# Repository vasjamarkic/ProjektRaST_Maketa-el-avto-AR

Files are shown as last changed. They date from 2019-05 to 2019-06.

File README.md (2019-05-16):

# ProjektRaST_Maketa-el-avto-AR
Projekt izdelave makete električnega vozila z LI-ion celicami in obogateno resničnostjo
ekipa
Z izdelavo makete smo začeli v novembru 2018, ko smo uspešno prijavili projekt na razpis RaST. Za delovanje 5 kW BLDC motorja smo načrtoval baterijski sistem z 140 Li-ion celicami, vezani v 10p14s konfiguraciji. Vse pridobljene celice iz odrabljenih prenosnikov, powerbank-ov in e-koles smo z Voltcraft merilcem temeljito testirali (polnjenje, praznjenje, polnjenje, notranja upornost, pregrevanje) in slabe izločili, dobre pa presortirali v skupine po podobnih kapacitetah. Nakup EV opreme je bil opravljen pri dobavitelju Miromax (Latvija), ostala oprema pa na eBay-u in lokalnih tehničnih trgovinah. Visokonapetostni sklop ima največjo napetost 58,8 V, zato smo izbrali polnilec takšne napetosti in motor s krmilnikom do napetosti 72 V. Sistem smo z glavno varovalko (ETI) omejili na 125 A, dodatno pa krmilnik sprogramirali na še nižji tok obratovanja. Krmilnik in motor vklopimo z obratom ključa na pozicijo M oziroma II; tako vklopimo glavni kontaktor, ki premosti napetost B+ baterijskega sklopa na krmilnik preko BMS enote. Tako na poziciji ključa I in II zunanji rele vklopi MCU (main control unit), to je glavna kontrolna enota ali računalnik avta/makete, kjer krmilnimo luči, varnostne sisteme, merimo temperature, napetosti 12V sistema ter B+ baterijskega sklopa motorja (preko IL300 linearnega optičnega pretvornika), vklapljamo/izklapljamo BMS, upravlja z Nextion display-om in komunicira z Raspberry PI (UART protokol) in krmilnikom motorja (SPI - CANbus modul za pretvorbo podatkov). Za vse to smo uporabili preprost Arduino UNO. V MCU-ju deluje samostojno Micro:bit razvojna ploščica, ki ima g-senzor za detekcijo trka; le ta izključi celoten pogonski sklop (izklopi glavni kontkator). Sistem ima še varnostno stikalo ob priključitvi AC kabla za napajanje (recharge) baterij ter "emergency stop" oz. odklopnik, ki ga lahko uporabnik sam ročno sproži v primeru nevarnosti. BMS enota poleg merjenja napetosti posemznih serij celic in temperatur seveda skrbi za varno delovanje pogona in omeji morebitne preobremenitve (tokovne, temperaturne, napetostne). Raspberry PI zbira vse podatke iz Arduina ter jih brezžično (WiFi) pošilja usmerjevalniku. Le ta ima nalogo, da podatke naprej posreduje odjemalcem; to so lahko pametni telefoni uporabnikov, s katerimi na maketi v povečani resničnosti (agumented reality ali AR) opazujejo v realnem času parametre na maketi in/ali spoznavajo delovanje in lastnosti/specifikacije posameznega sklopa EV (electric vehicle) oziroma makete.  
Na tej povezavi je prikazan proces izdelave makete - od načrtovanja, do izgradnje in preizkušanja:
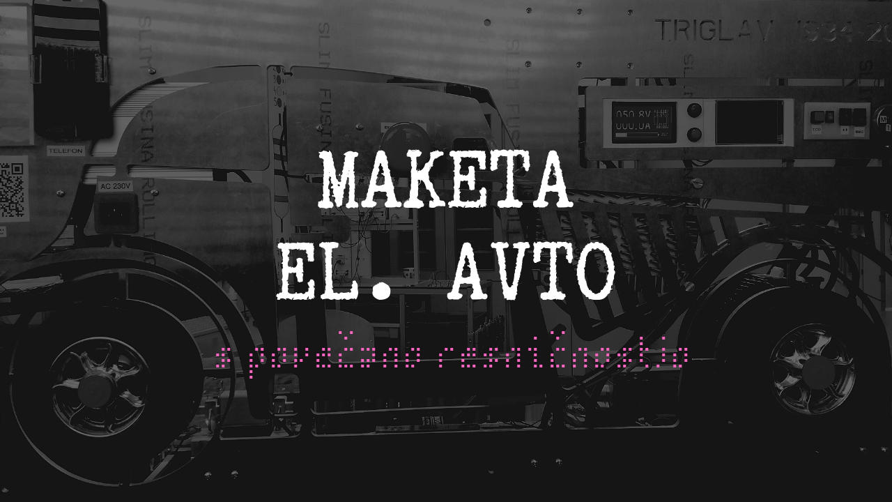
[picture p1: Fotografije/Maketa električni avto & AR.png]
IMAGE ALT TEXT (https://www.youtube.com/watch?v=B8ciZN42plY "Maketa el. avto")

Na spletni strani Srednje tehniške in poklicne šole Trbovlje je objavljen tudi opis projekta:
https://www.stps-trbovlje.si/category/rast/.

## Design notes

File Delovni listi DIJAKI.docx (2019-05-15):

# #rast – maketa el. avtomobila - NALOGE

## Arduino

### 1. Povezava med MCP2515 CAN/SPI modulom in Arduino Uno

a. Povežite pine Arduina Uno s pini modula MCP2515 CAN/SPI - izdelajte ustrezne priključke:

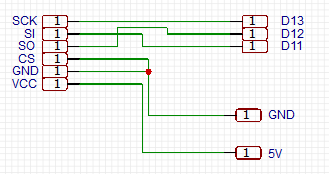
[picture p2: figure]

- 1x3p za priklop na Arduino,
- 1x6p ženski za MCP2515).
- 1x1p GND ženski,
- 1x1p 5V moški.

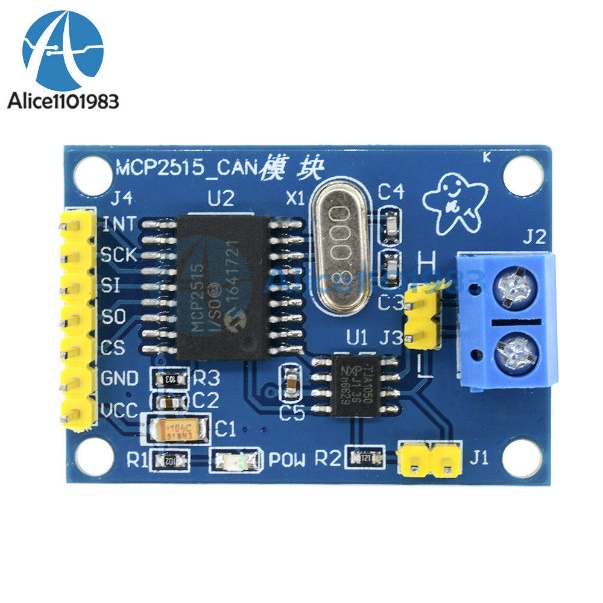
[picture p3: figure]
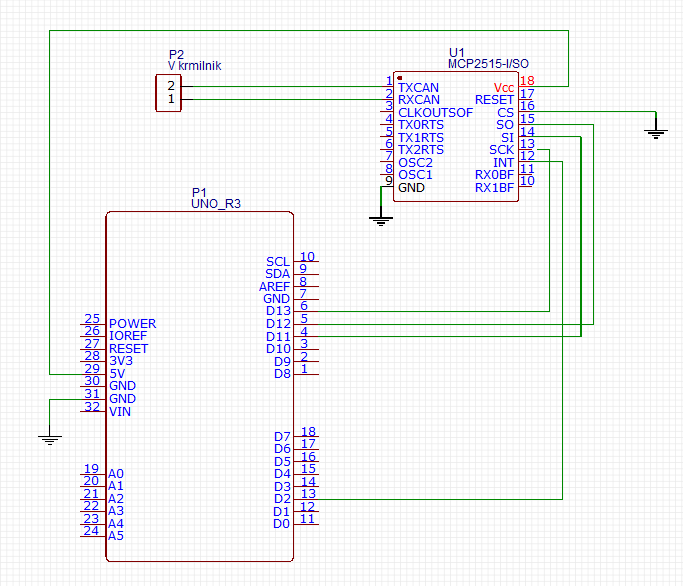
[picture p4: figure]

Vcc – 5 V; GND – GND; CS – GND; MISO – pin 12; MOSI – pin 11; SCK – pin 13

Opravljeno

b. Ustrezno podaljšajte CAN vodilo iz krmilnika motorja (uporabite dve žici in božirki) ter ga preko uvodnice vstavite v električno omarico. Na koncu namestite 2-pinski ženski konektor, ki paše na H-L moška pina modula MCP2515.

Opravljeno

c. Ustrezno sprogramirajte kodo Arduina, da bo lahko preko CAN vodila prejemal podatke iz krmilnika motorja. Primer inicializacija povezave SPI in CAN: [1] https://www.14core.com/wiring-the-mcp2515-controller-area-network-can-bus-diagnostics/

[2] https://www.electronicshub.org/arduino-mcp2515-can-bus-tutorial/a

Ni opravljeno

### 2. Vklop/izklop BMS-a z relejem z menjalnim stikalom na panelni plošči.

BMS se vklopi, ko je stikalo sklenjeno 3 sekunde, izključimo ga pa tako, če je stikalo sklenjeno 5 sekund. Za to bomo uporabili dvopoložajno stikalo: Arduino bo prebral stanje in krmilil rele, ki bo ustrezen čas sklenil »stikalo« BMS-a. Pozicija I – vklop BMS-a, pozicija II – izklop BMS-a. Stikalo ima tudi nevtralno pozicijo, katerega bomo vedno postavili takoj, ko bomo BMS vključili oz. izključili. Ker pa bi uporabnik na to pozabil, bi vključenost stikala na poziciji I ali II ne vplivala na ponovno aktivacijo releja za vklop/izklop BMS-a.

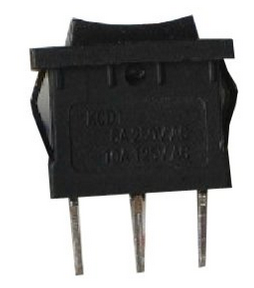
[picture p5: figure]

Na dig. vhoda (pin 6 in 7) Arduina povežemo skrajna priključka dvopoložajnega stikala (uporabite 2-polni moški konektor), sredinski priključek povežite na GND (0 V). Arduino pinout lastnost naj bo PULL_UP, torej ga proži GND brez pull-up uporov. V programu ustrezno definirajte oba digitalna pina kot vhod.

IN vhod releja priključite na pin 4 Arduina in ga definirajte kot izhod. Priključek DC+ releja vežete na +12V, DC- pa na GND. Na drugi strani releja povežete COM ter N.O. na priključke tipke BMS-a. Izvorno tipko BMS-a ohranimo!

vklop GND izklop

Opravljeno

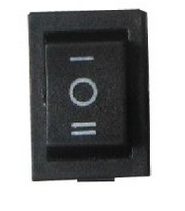
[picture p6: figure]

Izdelava kode/programa:

Ko uporabnik stikalo postavi na pozicijo I, Arduino vključi BMS – izhod postavi na visok nivo za 3 sekunde in ga nato postavi nazaj na nizki nivo. Ponovni vklop ni možen, dokler nista oba vhoda (pozicija I in II) na nizkem nivoju!

Ko uporabnik stikalo postavi na pozicijo II, Arduino izključi BMS – izhod postavi na visok nivo za 5 sekund in ga nato postavi spet na nizki nivo. Ponovni izklop ni možen, dokler nista oba vhoda (pozicija I in II) na nizkem nivoju!

Opravljeno

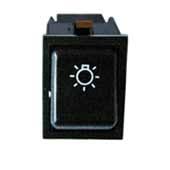
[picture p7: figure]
C:\Users\vasja.markic\AppData\Local\Microsoft\Windows\INetCache\Content.MSO\DB22575F.tmp

### 3. Vklop luči

Z ustrezno tipko na komandni plošči krmilimo prednjo in zadnjo luč makete avtomobila. Uporabimo ustrezni vhod na Arduino in dva izhoda za (direkten) vklop/izklop prednje ter zadnje LED luči. Na stikalu en priključek vežemo na GND, drugi pa na digitalni vhod Arduino.

Opravljeno

### 4. Povezava do Nextion display na Arduino

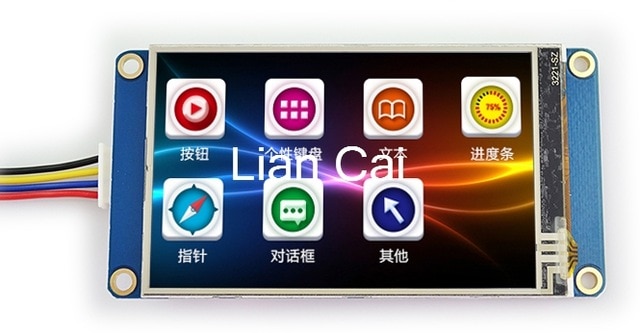
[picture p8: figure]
Rezultat iskanja slik za nextion display 3.5

Povežite žice iz Nextiona v MCU omarico :

- ČRNA – GND (na vijačno zbiralko)
- RUMENA in MODRA – Rx pin 0 in Tx pin 1 Arduino, uporabite moški 2 polni kontakt
- RDEČA – na 5 V, uporabite moški kontakt in ga vstavite v že uporabljeni 4-p konektor

Opravljeno

### 5. Programiranje Nextion display-a in Arduina

Vrednosti zajete iz temperaturnih senzorjev in optičnega linearnega ojačevalnika (napetost baterije) bomo prikazali kot grafične vrednosti – Gauges – na zaslonu, spodaj levo je primer:

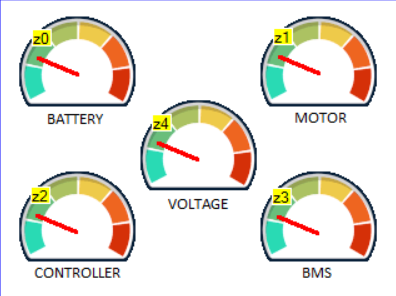
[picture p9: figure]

Pozor – prikazovalnik za napetost obarvajte po sledečem vrstnem redu (z leve proti desni): RDEČA, ORANŽNA, RUMENA, ZELENA, MODRA. Dodajte še napisa HIGH in LOW.

Uporabimo tako program Slikar za ustvarjanje png datoteke kot orodje Gimp za pomanjševanje slik iz spleta (tako ne kvarimo kvalitete pri pretvorbi dobljene slike). Velikost slike ozadja mora biti točno takšno, kot je velikost strani Nextion zaslona, to je 480 x 320.

Postopek v Nextion:

a. Zaženemo Nextion Editor in ustvarimo nov projekt, izberemo ustrezni zaslon (BASIC) NX…035, pod DISPLAY spremenimo orientacijo na 90 Horizontal.
b. V levem oknu Pictures dodamo našo ustvarjeno sliko ozadja s petimi grafičnimi zasloni (kliknemo gumb +).
c. V desnem oknu Page kliknemo objekt page0 in v spodnjem oknu Atribute objekt sta spremenimo v image. Dvokliknemo v spodnje prazno polje poleg pic in izberemo našo naloženo sliko ozadja. Sedaj bi morali videti v glavnem oknu Display naloženo fotografijo na zaslonu.
d. V levem oknu Toolbox kliknemo Gauge in ustrezno postavimo kazalec (po potrebi pomanjšamo/povečamo) na prvi grafični prikazovalnik. V oknu Atribute mi spremenimo še barvo in debelino kazalca (pco in wid). Obvezno mu moramo še spremeniti ozadje: lastnost sta spremenimo v crop image, v prazno polje picc pa izberemo enako sliko ozadja kot pri točki c.
e. Ustvarjeni gauge copy/paste na še preostale grafične prikazovalnike. Zapišite si vrednost id in objname vsakega prikazovalnika/gauge, saj jih boste tako naslavljali v programski kodi Arduino.
f. Kliknite Compile.
g. Kliknite File → Open build Folder in prekopirajte nastalo binarno datoteko na mikro SD kartico (s pomočjo in adapterja). Na kartici mora biti samo ENA datoteka! Ustavite mikroSD kartico v (ugasnjen) Nextion display, priklopite napetost (5V, GND), počakajte, da Nextion naloži datoteko, izklopite napajanje, PRITISNITE mikroSD kartico navznoter, da jo lahko izvlečete ven in ponovno priključite napajanje Nextion-u. Sedaj bi morali videti vašo sliko na Nextion zaslonu.
h. Sedaj priključite tudi RX in TX pina iz Nextiona na Arduino pin 0 in 1 (Rx gre na Tx in Tx gre na Rx!).

Programiranje v Arduino:

a. Na spletu poiščite ITEADlib knjižnico in jo namestite v Arduino okolje.
b. Na začetku kode dodajte naslednje knjižnice:

#include <NexConfig.h>

#include <NexPicture.h>

#include <NexGauge.h>

#include <Nextion.h>

#include <NexTouch.h>

#include ''Nextion.h''

Nato deklarirate grafične prikazovalnike:

NexGauge z0 = NexGauge(0, 1, ''z0'');

NexGauge z1 = NexGauge(0, 2, ''z1'');

Itd ..

Kjer je prvi parameter v oklepaju številka strani, drugi parameter ID objekta, tretji pa objname.

c. V razdelki programa void setup() inicializirajte Nextion zaslon z ukazom:

nexInit();

d. V glavni zanki void loop() vrednosti preko UART prenašamo na Nextion z ukazom:

z0.setValue(T3);

Torej prvi prikazovalnik (z0) naj pokaže vrednost spremenljivke T3. Pozor – če je T3 na primer 60 °C, se bo prikazovalnik pomaknil na kot 60 ° → potrebo je preskalirati vrednost, na primer temperatura 90°C bo na prikazovalniku imela odklon 180°!

e. Podobno uredite prikaz za ostale temperature.
f. Pri prikazu napetosti (z4) želimo, da pri 42 V je kazalec na 0°, pri 58 V pa na 180°!

### 6. Vklop ventilatorja ob prekoračitvi temperature

Dopolnite kodo tako, da ob prekoračitvi temperature 40 °C se vklopi ventilator (krmiljen preko rele FAN) za hlajenje baterij. Ko temperatura pade pod 40°C, se ventilator ugasne.

Opravljeno

### 7. Merjenje napetosti na baterijskem modulu

Baterijski Li-Ion modul mora biti galvansko ločen od ostalih elektronskih komponent (MCU, 12V sistem, Raspberry ..), tudi GND glavne baterije je galvansko ločen od ostalih ozemljitev!

[1] https://www.digikey.com/en/articles/techzone/2012/dec/linear-optical-isolation-for-safe-sensor-operation

[2] https://www.vishay.com/docs/83708/appnote50.pdf

Uporabimo linearni opto-izolator IL300 v povezavi z operacijskim ojačevalnikom LM393:

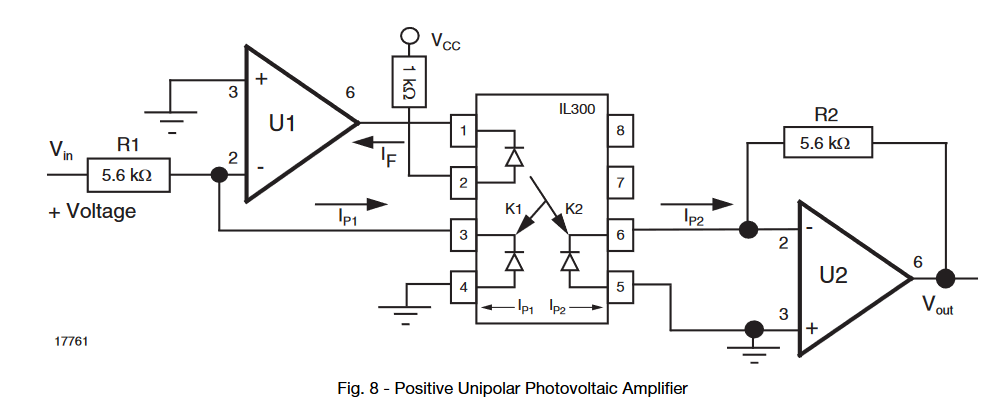
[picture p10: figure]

Vezje izdelajte na testni ploščici; uporabite ustrezne elemente in tudi konektorje za priklop pinov – za vhodne (Vin, Vcc, GND1) moške pine, za izhodne (Vout, GND2) pa ženske. Prejšnja sonda, ki vsebuje delilnik napetosti in tri žice je potrebno predelati – uporabimo le žico za GND (na GND2) ter žico, ki pelje na analogni vhod Arduina A0. Le tega boste priklopili na Vout (na shemi).

B+ glavne baterije (iz glavne varovalke) bomo priključili na Vin , za Vcc pa bomo izdelali uporovni delilnik, ki bo znižal napetost (med 10 V in 30 V). Prav tako mora levi operacijski ojačevalnik LM393 biti napajan z isto Vcc napetostjo.

Na pin 2 mora biti upor takšne vrednosti, da bo IF reda 10 mA (max 60 ma), torej je R=Vcc/10mA. Napetost VF na LED diodi je tako 1.25 V.

Postopek izračuna uporov R1 in R2 pa po sledečih korakih:

1) Ugotovite lastnosti OO (Iout) ter IL300 (K1, K2, K3, Vin, G – vaš željeni faktor ojačanja)
2) Izračunamo Ip1 = K1×Ioutmax
3) R1=Vin/Ip1
4) R2=(R1×G)/K3, če je G=Vout/Vin

Ni opravljeno

## Krmilnik in motor

### 1. Osnovne lastnosti krmilnika

Izdelajte/prevedite dokumentacijo za nastavitve in prvi zagon motorja s krmilnikom – prav tako na PC namestite ustrezen program za diagnostiko motorja, ki ga boste upravljali preko USB/RS232 vodila.

Ni opravljeno

[1] https://kellyev.com/shop/kls-mn/

### 2. Pedal za zavoro

Uporabite potenciometer ter pozicijsko tipko za simulacijo zaviranja. Analogni signal iz krmilnika je povezan na potenciometer poleg napajanja in GND, za pozicijsko stikalo, ki javlja pritisnjen pedal pa dve žici iz krmilnika (napajanje in digitalni vhod). Uporabite 5-polni IP67 konektor.

Ni opravljeno

### 3. Prvi zagon motorja

#### Identification angle operation

Na začetku moramo izvesti detekcijo kota preden zaženemo motor. To storimo s pomočjo programa na PC-ju ali ali aplikacije na pametnem telefonu/tablici. Privzeta izbira senzorjev motorja so halove sonde, izbira je 2 (speed sensor type).

Postopek:

1. Na motor ne montirajte nobenih gredi, menjalnika ali koles (bremena). Krmilnik je povezan na baterje, stikalo za vklop, motor in pedal za pospeševanje (glej shemo):

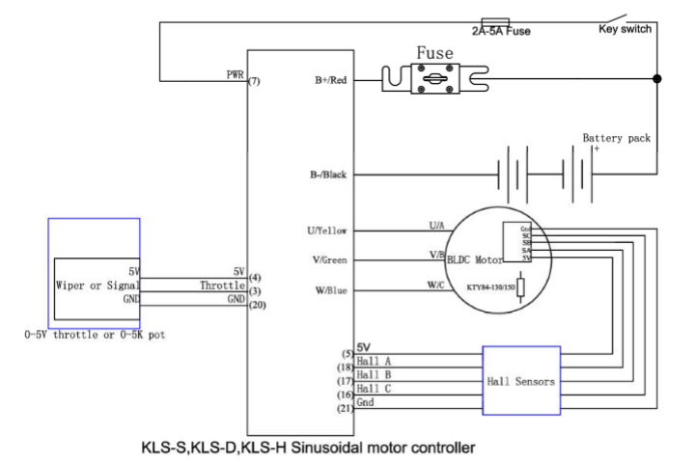
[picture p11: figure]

2. Povežite krmilnik z PC-jem (ali tablico) z USB na RS232 kablom. Med krmilnikom in RS232 kablom je vmesni adapter SM-4ADB9(RS232). Če uporabljate tablico ali telefon uporabite Z-TEK USB to RS232 kabel.

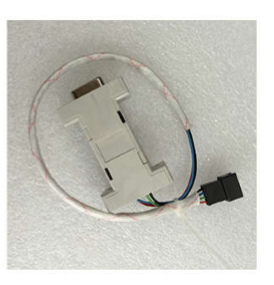
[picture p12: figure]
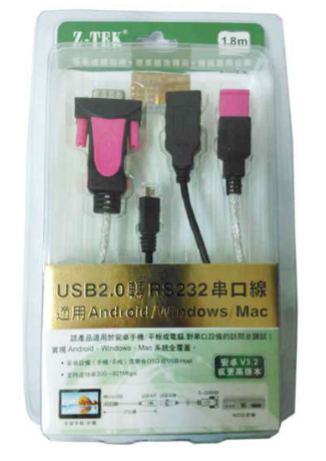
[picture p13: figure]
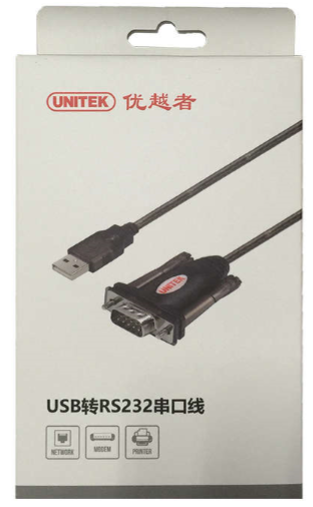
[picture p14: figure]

Z-tek (za telefon) USB na RS232 (za PC) SM-4ADB9(RS232) (na krmilnik)

3. Naložite ustrezen program na PC ali telefon/tablico za vaš krmilnik: www.kellycontroller.com/support.php
4. Vključite krmilnik tako, da bo krmilnik vklopljen (pin 7 na napajalno napetost) ter priključka B- in B+ sta pod baterijsko napetostjo (vklopimo glavni kontakor). POZOR! Ali imata kontaktor in zasilno stikalo vzporedno vezana upora? Preverite!

Zaženite program za diagnostiko krmilnika. Kliknite na gumb Read. Pojavila se bo prvo okno programa:

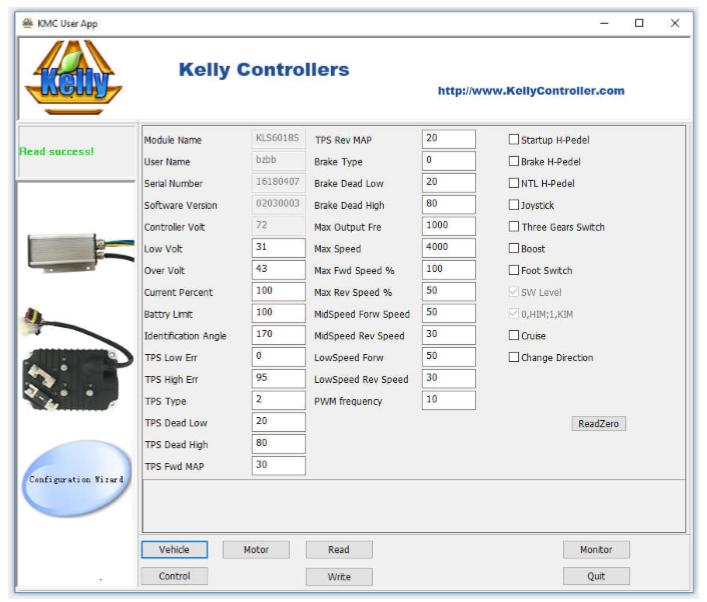
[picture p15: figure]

Preverite vrednost parametra Identification angle. Pravilna vrednost parametra je 85. ta vrednost pomeni, da je motor že opravil detekcijo smeri s krmilnikom, vendar je to tovarniška nastavitev. Vaš motor je drugačen od testnega, zato morate detekcijo ponovno opraviti.

5. V polje Identification anlge vpišite vrednost 170 in kliknite Write. Program bo javil okno z obvestilom, da je bilo zapisovanje uspešno (Write operation successful). Zaprite program z gumbom Quit. Izključite napajanje krmilnika.
6. Počakajte nekaj sekund in ponovno vključite napajanje. Piskač bo javljal neprekinjen zvok in motor se bo začel vrteti v različne smeri. Tako krmilnik opravi detekcijo smeri/kota.
7. To traja 2 do 3 minute, zato počakajte.
8. Ko je detekcija kota/smeri končana, piskač preneha s piskanjem. Nato bo piskalo v zaporedju, ki pomeni neko napako. Ponovno zaženite program – na zaslonu boste videli sporočila o napakah.
9. Ponovno ugasnite krmilnik. (Zaprite tudi program). Počakajte nekaj sekund, preden ponovno še enkrat prižgete krmilnik.
10. Ponovno vklopite krmilnik in program. V polju Identification Angle bi moralo ponovno pisati vrednost 85. V tem primeru je detekcija kota/smeri uspela. Krmilnik je sedaj pripravljen za uporabo in krmiljenje motorja.
11. V kolikor ni reset error code, bo vrednost ostala pri 170. Krmilnik še zmeraj ugotavlja detekcijo smeri.
12. Nikakor ne poskušajte sami zapisati vrednost 85 v to polje, ali resetirati napajanje, če ne vidite kakršne koli sporočila o napakah!
13. Če pisanje traja več kot 5 minut pri detekciji kota in se pojavijo druge napake v programu, preglejte še enkrat povezave (sploh pri senzorjih) in zapišite vrednost 85. ???? Vrednost 170 ne sme ostati v primeru, če želite izklopiti napajanje. ????

Sicer bo krmilnik ponovno poskušal opravljati identifikacijo kota/smeri.

Ko se pojavijo okna z napakami, kliknite Quit in ponovno začnite s točko 6.

14. Vrednost 170 ne sme biti zapisana preden ponovno vključimo napajanje po uspešno opravljeni identifikaciji.
15. V kolikor smer vrtenja in prava, enostavno omogočite Change Direction polje na prvi strani okna programa. Klinite Write. Ponovno resetirajte napajanje. Motor se bo nato vrtel v obratno smer od prejšnje.

Uporabljajte funkcijo Identify za motor in za halove sonde v programu!

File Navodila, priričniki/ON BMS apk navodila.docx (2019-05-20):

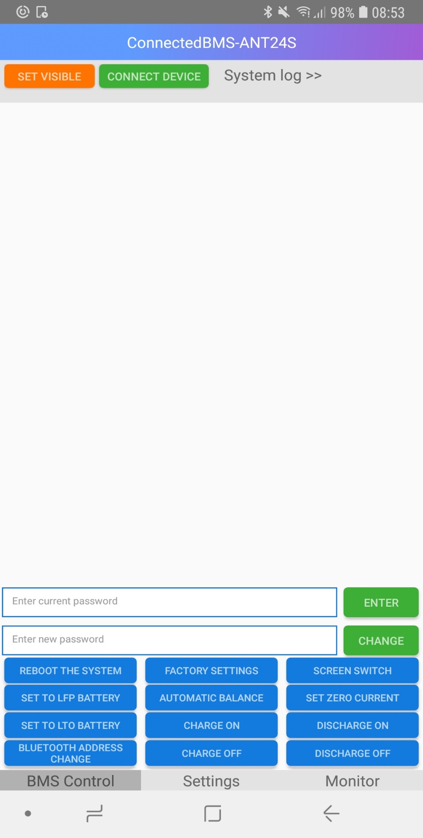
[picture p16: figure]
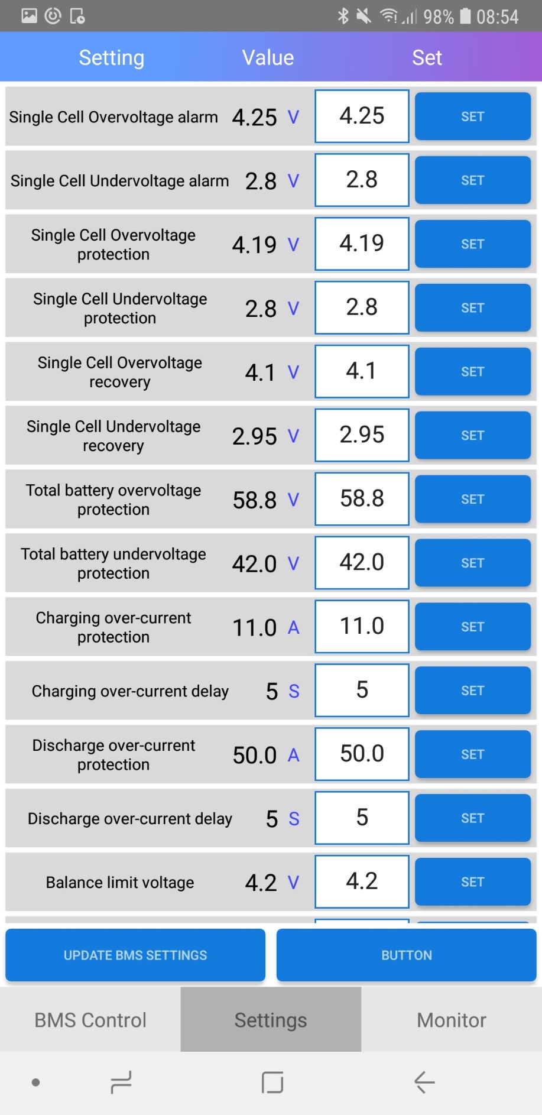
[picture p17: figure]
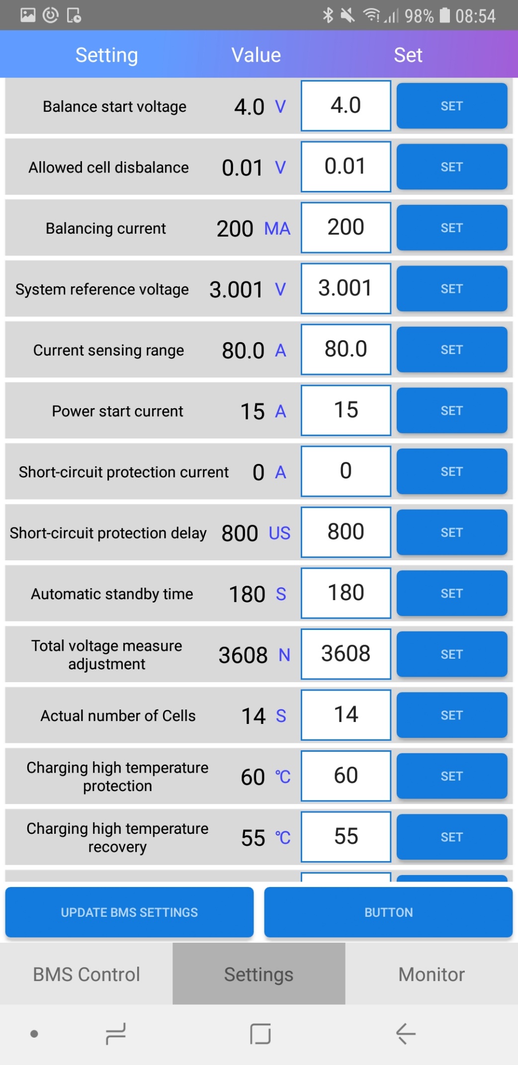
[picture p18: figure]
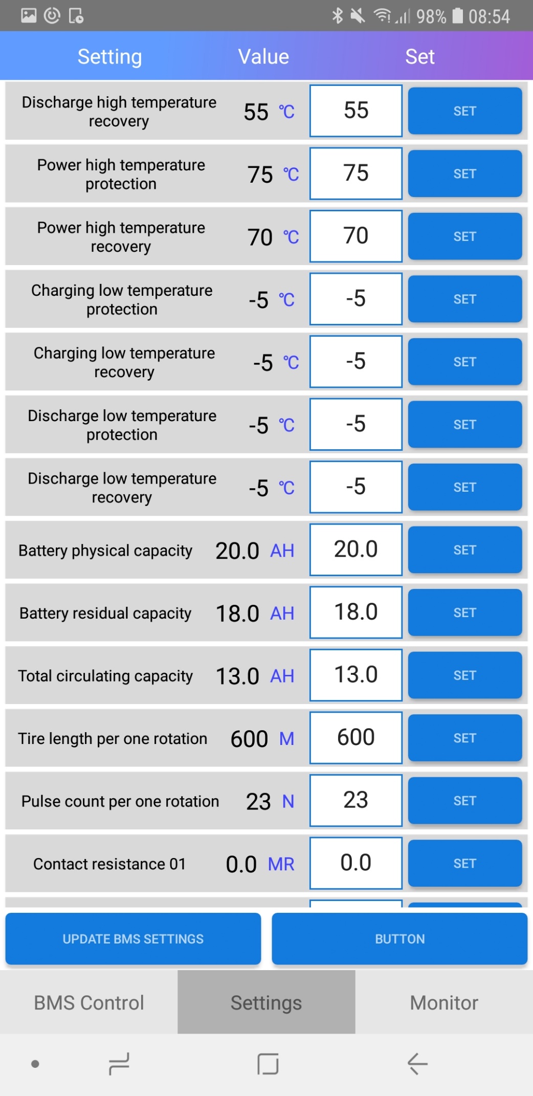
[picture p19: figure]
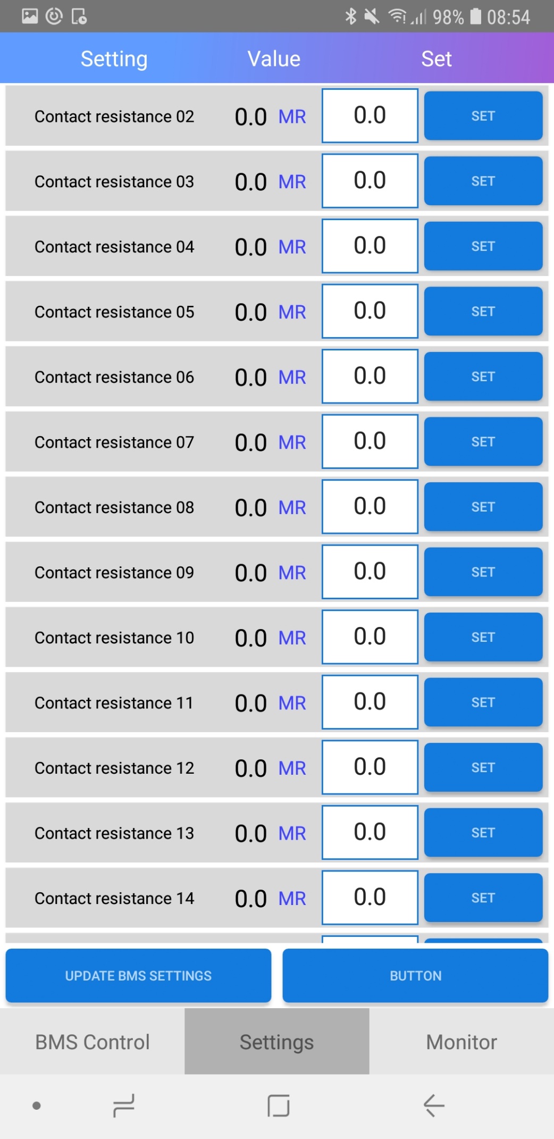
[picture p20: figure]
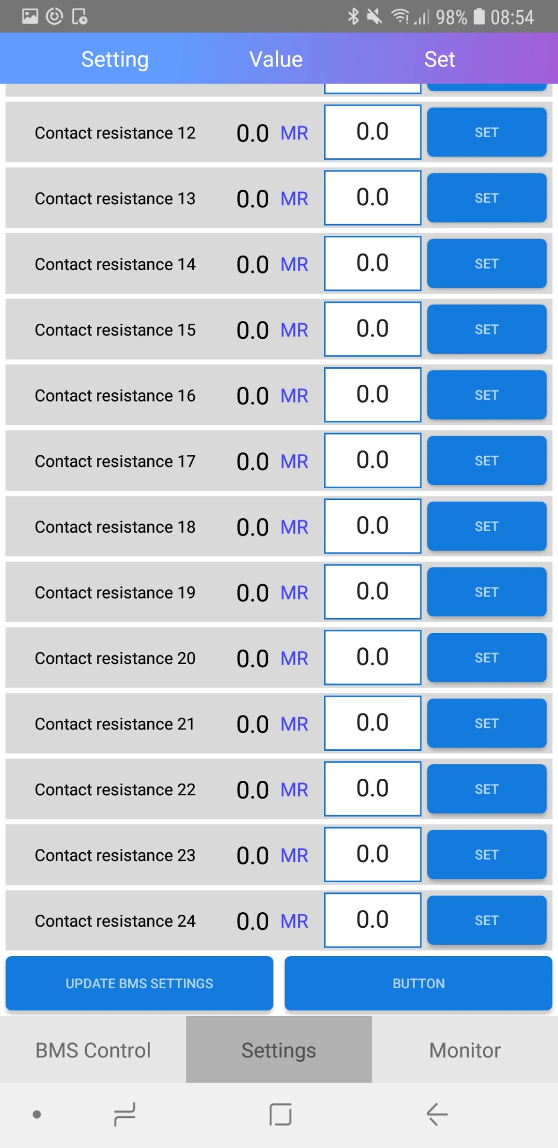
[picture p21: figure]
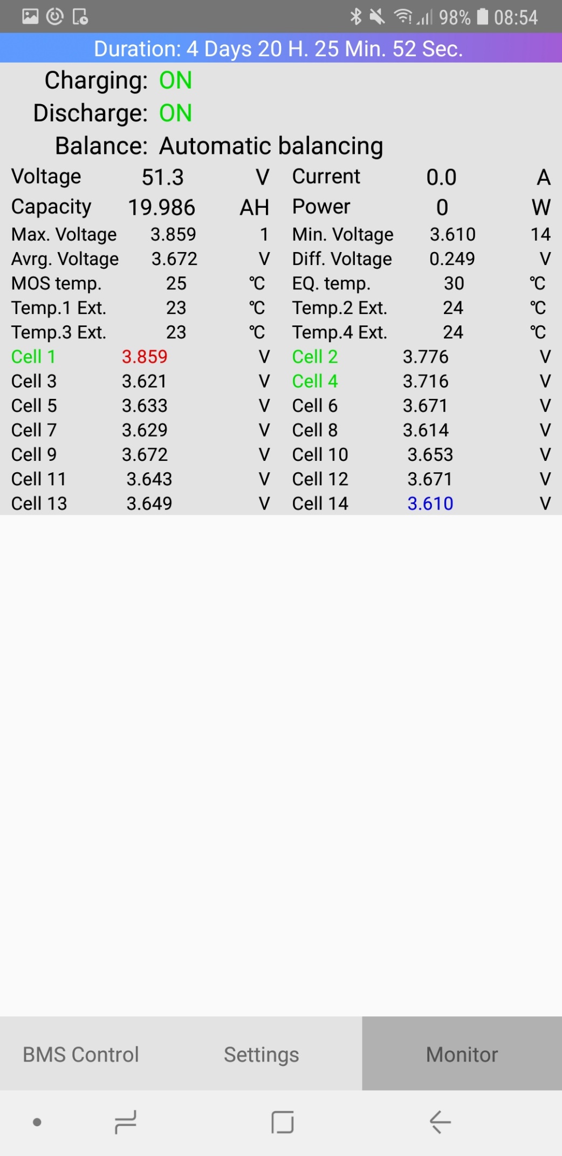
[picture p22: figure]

ON BMS apk za Android

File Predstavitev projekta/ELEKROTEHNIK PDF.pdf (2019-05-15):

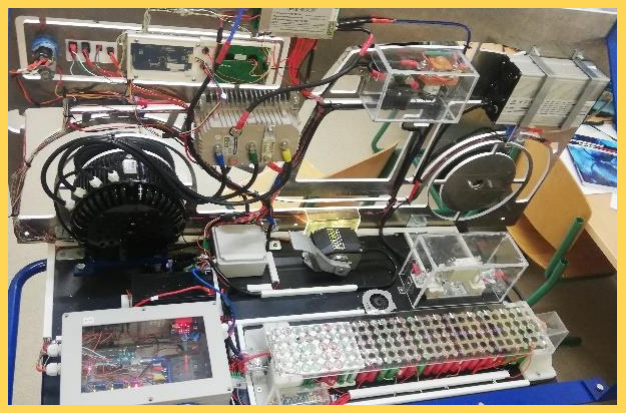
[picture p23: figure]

### E L E K T R O T E H N I K

Kristian Pavlin, Marko Žuželj, Nejc Sardinšek in Žiga Košir

Mentor: Vasja Markič

Elektrotehniki smo se dela lotili na dveh frontah; Vsako vozilo v današnjem času ima svoje »možgane« ali MCU – main control unit, torej
mikroračunalnik, | ki | nadzoruje | vse | vitalne
parametre in funkcije vozila (meritve temperature, napetosti …) ter upravlja za aktuatorji (vklop sistema in relejev aktuatorjev, izklop sistema ob trku itd). Tako smo uporabili različna orodja in sisteme, kot so Arduino, Micro:Bit ter Nextion za prikaz parametrov in izvajanje meritev.
Drugi skupina dijakov je izdelala načrt in osnovala postavitev in priključitev vseh EV (electric vehicle) komponent: BLDC motor, krmilnik, kontaktor, odklopnik za izklop v sili, glavno varovalko, BMS enoto, polnilec in li-ion baterijski sklop. Baterijske celice smo s pomočjo lokalne akcije zbrali iz odrabljenih prenosnikov in električnih koles, jih vseh 140 testirali in ponovno povezali in točkovno privarili s posebno varilno napravo.
Ko je bila baterijska enota testirana in zvezana, smo povezali vse EV elemente in postopoma priključevali enote: najprej BMS oziroma battery management system, nato polnilec in končno še krmilnik z BLDC motorjem. BMS enoto smo
konfigurirali | na | pametnem | telefonu | preko
bluetooth | povezave, | krmilnik | motorja | pa
sprogramirali s prenosnikom preko serijskega komunikacijskega protokola RS232.
Vsi ti podsistemi tako delujejo povezani kot celota in skrbijo za varnosti in pravilno delovanje motorja.

## Projekt RaST – Maketa električnega avtomobila z obogateno resničnostjo (AR)

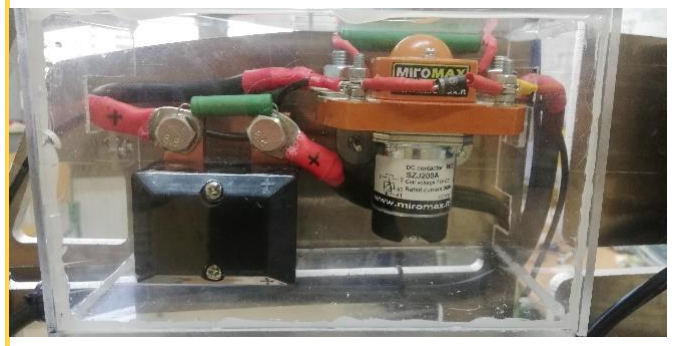
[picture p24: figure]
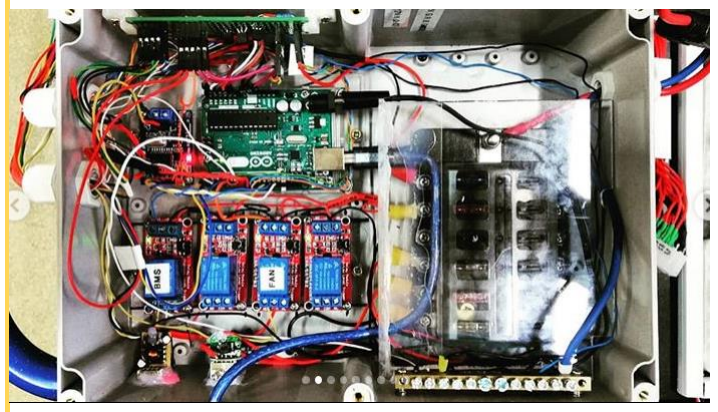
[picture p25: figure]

2

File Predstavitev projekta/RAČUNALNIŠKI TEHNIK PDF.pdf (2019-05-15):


### T E H N I K R A Č U N A L N I Š T V A

Miha Krajnc, Denis Funkel in Klemen Šuštar Mentor: Žiga Podplatnik

Tehniki računalništva smo za potrebe projekta razdelili delo na dva segmenta: V prvem smo se ukvarjali in razvili sistem za prikaz obogatene resničnosti. S pomočjo telefona lahko prikazujemo realne podatke na posameznih sklopih makete, kot so priključene enote, temperature in napetosti baterij. Zato smo na mikroračunalniku Raspberry Pi namestil ustrezen operacijski sistem, na katerem ta enota sprejema podatke iz serijskega vmesnika UART, ki jih priskrbi razvojna plošča Arduino – le to so sprogramirali dijaki iz programa Elektrotehnike. Te podatke nato obdelamo in jih shranimo v podatkovno bazo, ki je nameščena na Raspberry Pi-ju. Da se lahko podatki tudi prikažejo na zaslonu kateregakoli uporabniškega telefona, smo morali opraviti konfiguracijo usmerjevalnika. Podatki se nato prikazujejo ob komponentah v navideznem svetu obogatene resničnosti.


V drugem segmentu so dijaki delali na zaslonu Nextion. Za prikazovanje podatkov so oblikovali grafični vmesnik ter s pomočjo programske kode poskrbeli, da se podatki, ki jih zajema Arduino, pravilno prikazujejo preko uporabljenih knjižnic in UART protokola. Zaslon prikazuje tudi vklop luči, javlja nizko napetostno stanje 12 V baterije ter vklop ventilatorja ob povečani temperaturi Li-ion baterij, poganjajo BLDC motorja.

## Projekt RaST – Maketa električnega avtomobila z obogateno resničnostjo (AR)



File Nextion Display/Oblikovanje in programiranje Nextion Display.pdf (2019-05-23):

# Oblikovanje in programiranje Nextion Display-a

## Projekt RaST


Mentor: Vasja Markič, Marjan Pograjc, Žiga Podplatnik | Denis Funkel, Klemen Šuštar 3.C

1. Ustvarjanje projekta
a. Projekt ustvarimo tako, da v zgoraj levo kliknemo na »File« in izberemo opcijo »New«


b. Odpre se nam pojavno okno, vanj vpišemo kako se bo projekt imenoval in pritisnemo »Shrani«


c. Ko projekt shranimo se odpre drugo pojavno okno, v katerem izberemo model in orientacijo zaslona.
2. Dodajanje in nastavljanje slik
a. V spodnjem levem kotu je okno v katerem lahko dodajamo, brišemo in spremenimo slike.
b. Dodajanje slike v projekt

Z znakom »+« dodamo slike. Ko ga pritisnemo se odpre pojavno okno, v katerem izberemo poljubne slike iz mape, ki smo jo izbrali. Za izbor več slik na enkrat lahko držimo tipko »CTRL« med tem ko klikamo na slike.

+ … dodajanje slik

- … brisanje slik

… zamenjava že dodane slike
↑ ↓ … spreminjanje indexa (zaporedja) slike gor ali dol 🗑️… brisanje slik

↶
⤻

c. Dodajanje slike za ozadje

Najprej moramo spremeniti »sta« na opcijo image. Ko to naredimo, kliknemo dvakrat na »pic«, da se nam odpre okno za izbiro slike in izberemo sliko ozadja.
!!! Ozadje mora biti iste velikosti, kot je velikost zaslona !!!


3. Gradniki, ki so bili uporabljeni v projektu
a. Progress bar


b. Guage


c. Image

»dez« … orientacija, vodoravno/navpično

»bpic« … slika ozadja, ki je enaka velikosti objekta

»ppic« … slika ospredja, ki je enaka velikosti objekta

»val« … privzeta vrednost

»sta« … nastavimo na »crop image«


»picc« … za sliko izberemo ozadje, ki je enake velikosti kot zaslon

»pco« … barva kazalca

»wid« … širina kazalca


»pic« … slika, ki je enaka velikosti objekta

4. Končni izgled


Gradniki:

j0 – j3: Progress bar (Prikazovalniki temperature)

j4 – j5: Progress bar (Indikatorji stanja)

p0 – p5: Image (Ikone in besedilo v obliki slik)

z0: Gauge (Števec za prikaz napetosti baterije)

Vse ostalo, kar vidite na display-u je slika v ozadju.

5. Programiranje zaslona z Arduinom

#include <NexGauge.h>

#include <NexPicture.h>

#include <NexProgressBar.h>

NexProgressBar j0 = NexProgressBar(0, 1, "j0"); // inicializacija gradnika NexProgressBar ([id_strani],[id_gradnika],[ime_gradnika])

NexGauge z0 = NexGauge(0, 5, "z0");

void setup(){

}

void loop() {

j0.setValue(spremenljivka_1); // prvo vrednost nastavimo dvakrat zaradi napake v knjižnici

j0.setValue(spremenljivka_1);

z0.setValue(spremenljivka_2);

}

spremenljivka_1 … int (celoštevilska številka) od 0 do 100

spremenljivka_2 … int (celoštevilska številka) od 0 do 360 (v našem primeru od 0 do 180)

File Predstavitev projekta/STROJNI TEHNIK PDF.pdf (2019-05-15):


S T R O J N I T E H N I K

Matic Zamuda in Matej Strniša Mentor: Marjan Pograjc

Izdelali smo maketo 1. slovenskega avtomobila, ki ga je snoval Stanko Bloudek, zato ime Triglav. Tako smo povezali zgodovinskega dejstva z novo tehnologijo električnih vozil.
Bloudek je leta 1933 postal solastnik in glavni konstruktor družbe Automontaža, ki je z različnimi imeni obstajala vse do stečaja leta 2002 in bila tako najstarejše avtomobilsko podjetje v Sloveniji. Podjetje se je ob Bloudkovem prihodu ukvarjalo s predelavo avtobusov in izdelavo karoserij za tovornjake. Motorje so kupovali pri Mercedesu, Henschlu in Deutzu in jih nadgrajevali z lastnimi karoserijami.
Bloudek je pri Automontaži zasnoval in izdelal prvi slovenski avtomobil z imenom Triglav. Izdelal ga je na podlagi DKW-jevega dvotaktnega motorja, cena pa je bila 40 tisoč takratnih dinarjev. Potem, ko so leta 1934 predstavili njegov prototip, so morali serijsko proizvodnjo žal opustiti. Enako se je zgodilo tudi z načrtovanim razvojem lastnega zračno hlajenega motorja.


Strojni tehniki smo izrisali konstrukcijo, po izdelanih načrtih smo naročili izrez silhuete avtomobila na aluminijasti plošči in mehanske komponente montirali ploščo ter na nosilno konstrukcijo. S 3D tiskalnikom smo stiskali manjkajoče sestavne dele in potrebne mehanizme. Prav tako smo izdelali tehniško dokumentacijo.

## Projekt RaST – Maketa električnega avtomobila s obogateno resničnostjo (AR)


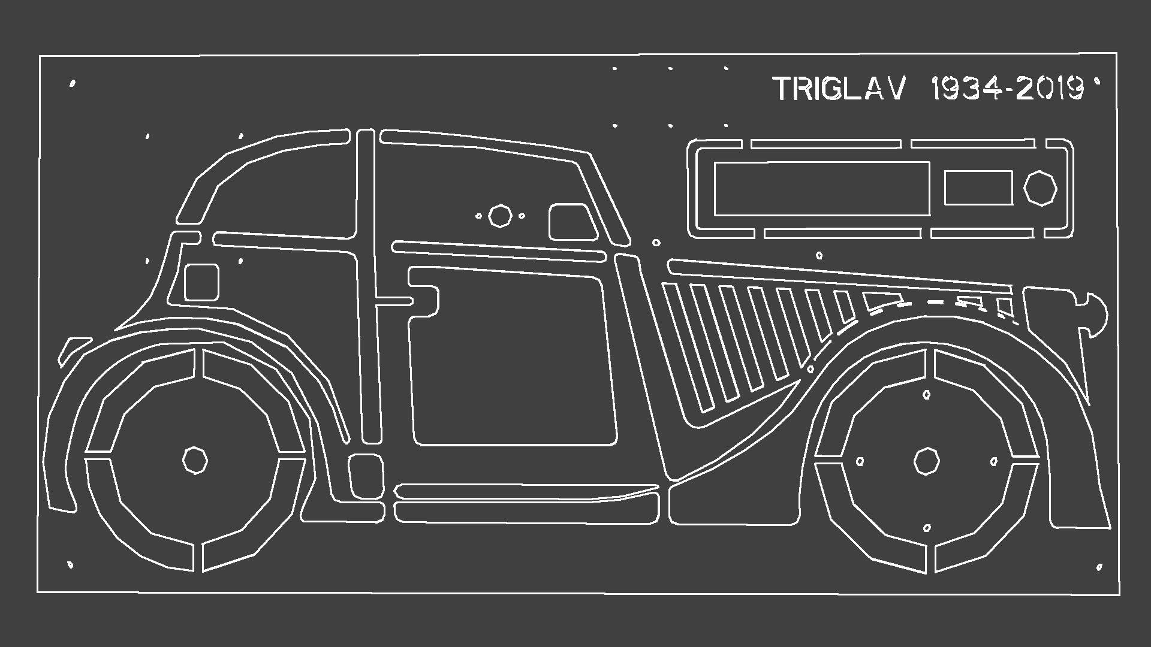
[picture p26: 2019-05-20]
AplikacijaAR/tarcaZaznavanja.png

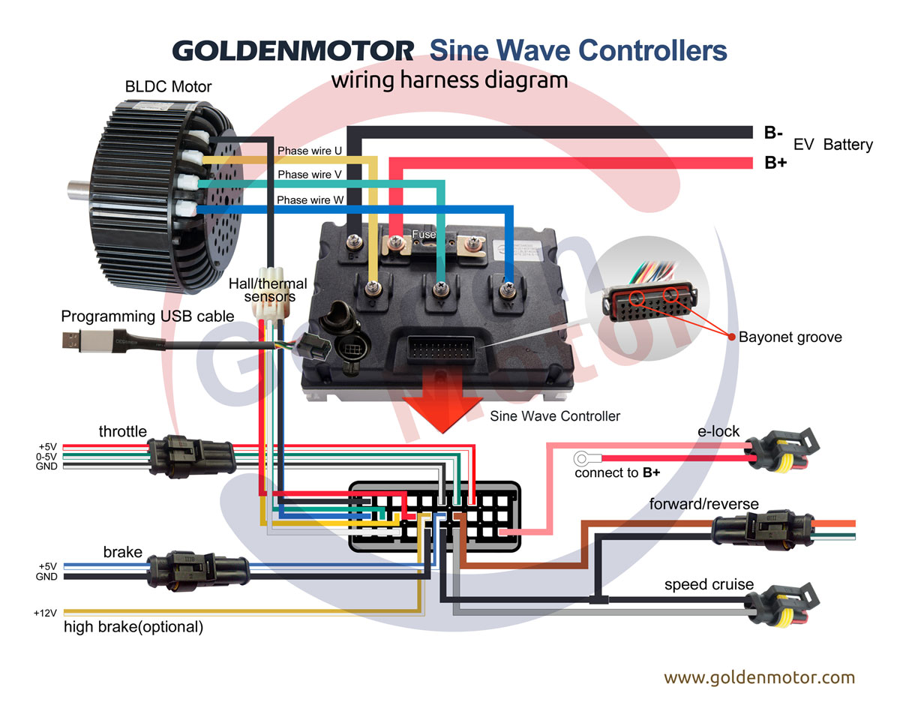
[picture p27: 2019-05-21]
Navodila, priričniki/NAČRT vezave motorja s krmilnikom.jpg

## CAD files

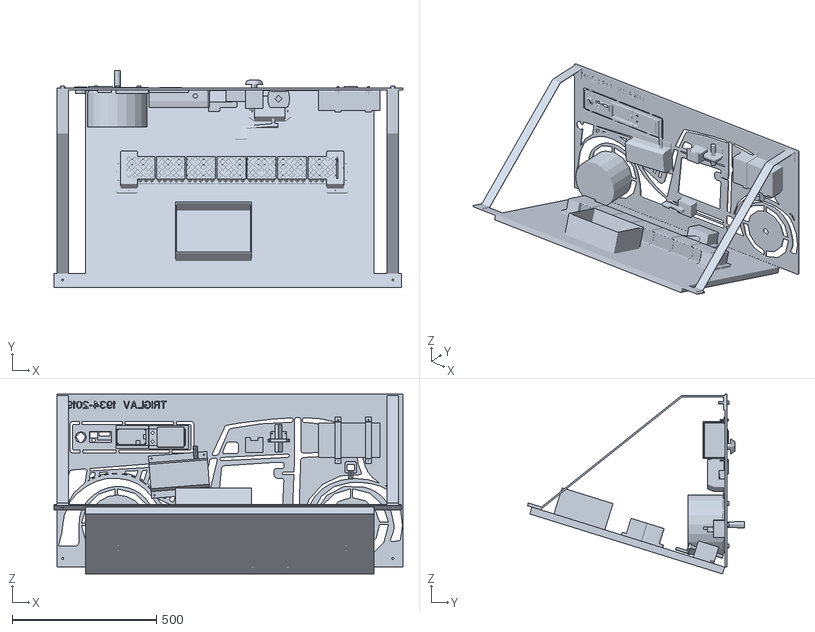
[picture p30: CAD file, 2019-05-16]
STL/triglav_11.stl
1210.0 x 752.2 x 623.9

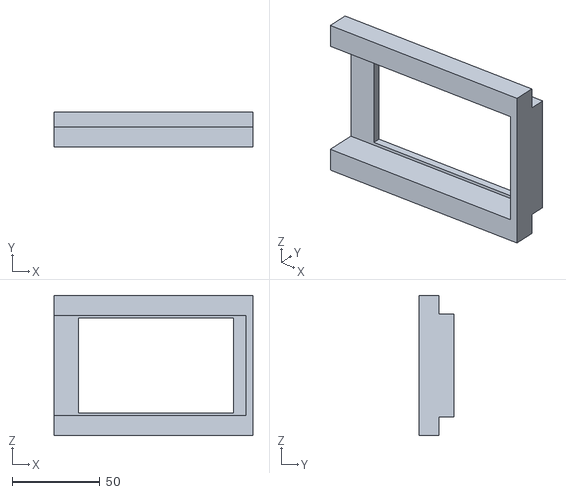
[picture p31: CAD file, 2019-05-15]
STL/nosilec_display1.stl
113.5 x 20.0 x 80.0

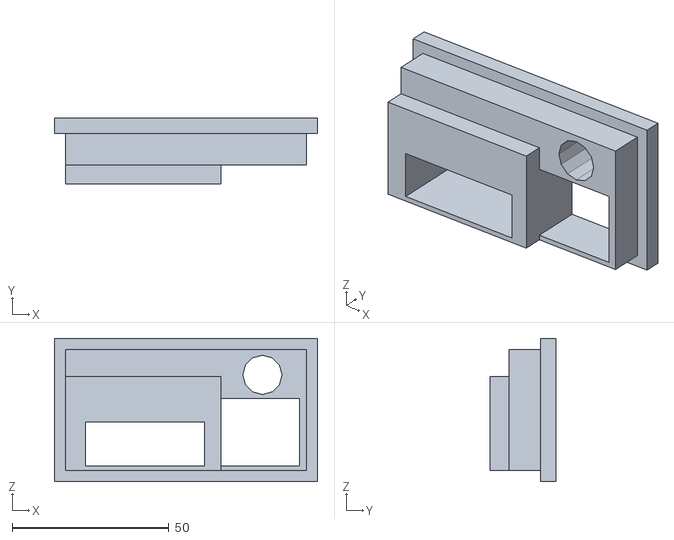
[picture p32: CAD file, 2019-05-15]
STL/nosilecstikal1.stl
83.8 x 21.0 x 45.6

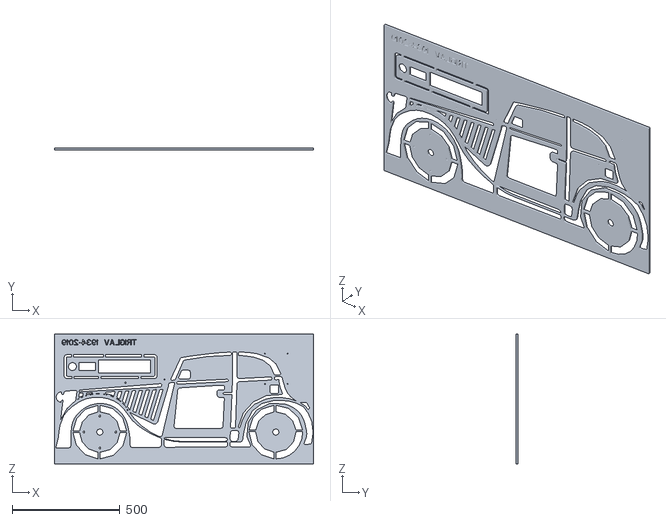
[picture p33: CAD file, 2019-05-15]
STL/elavto.stl
1200.0 x 8.00 x 600.0

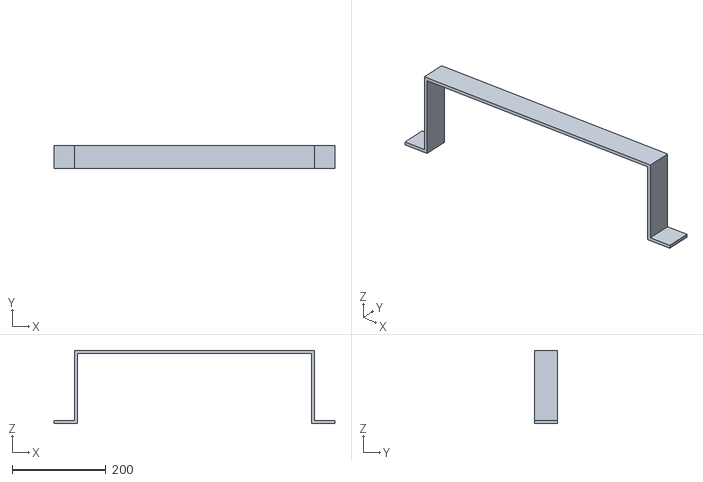
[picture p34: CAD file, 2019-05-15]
STL/nosilec.stl
600.0 x 50.0 x 156.0

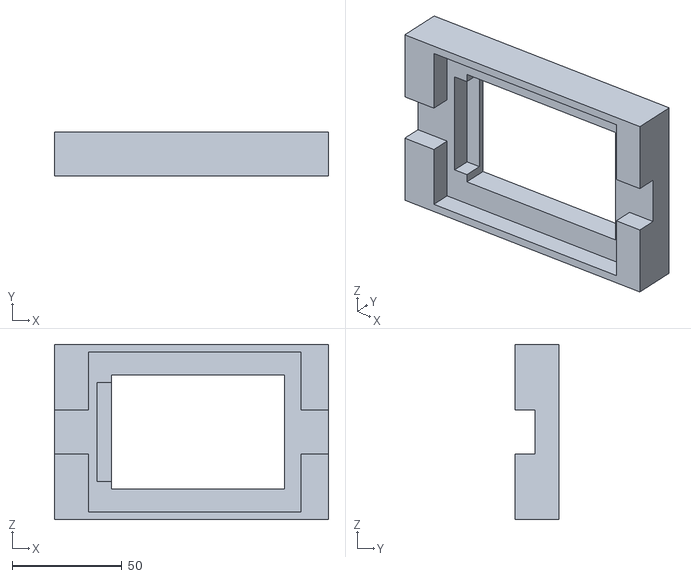
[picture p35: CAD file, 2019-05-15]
STL/nosilce_display.stl
125.0 x 20.0 x 80.0

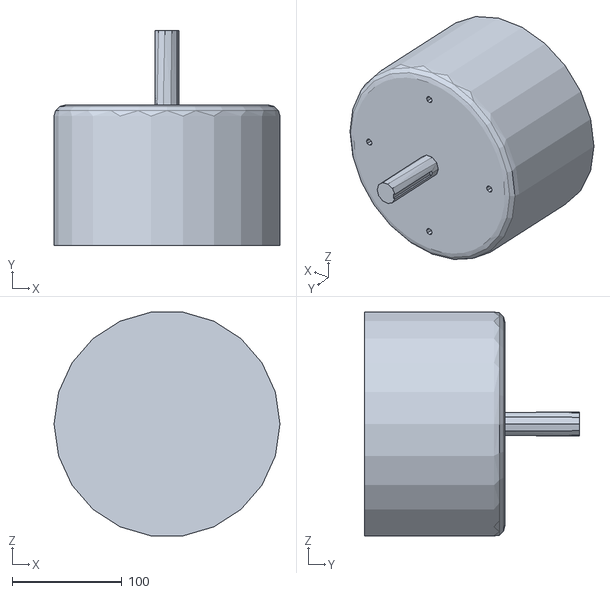
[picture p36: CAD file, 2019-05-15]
STL/motor.stl
206.0 x 196.0 x 203.9

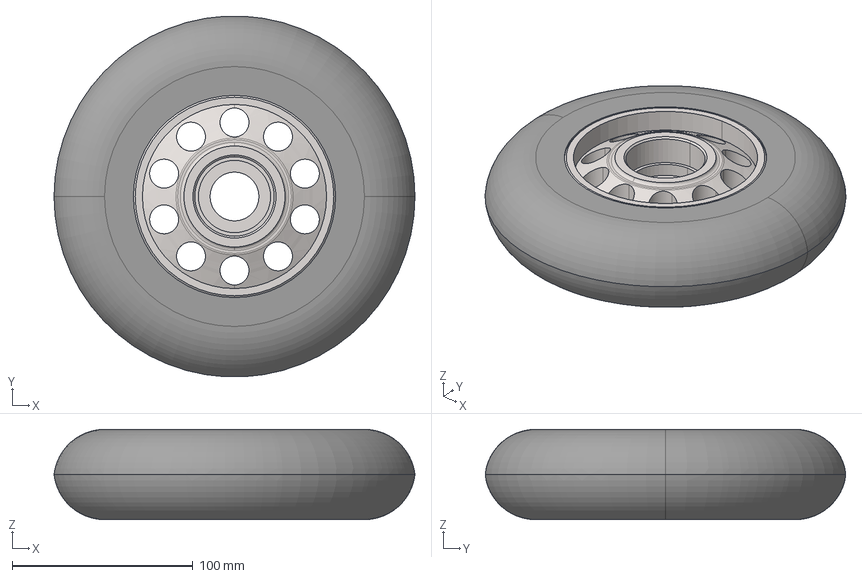
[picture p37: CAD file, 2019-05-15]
STL/kolo.stp
200.0 x 199.7 x 50.0 mm

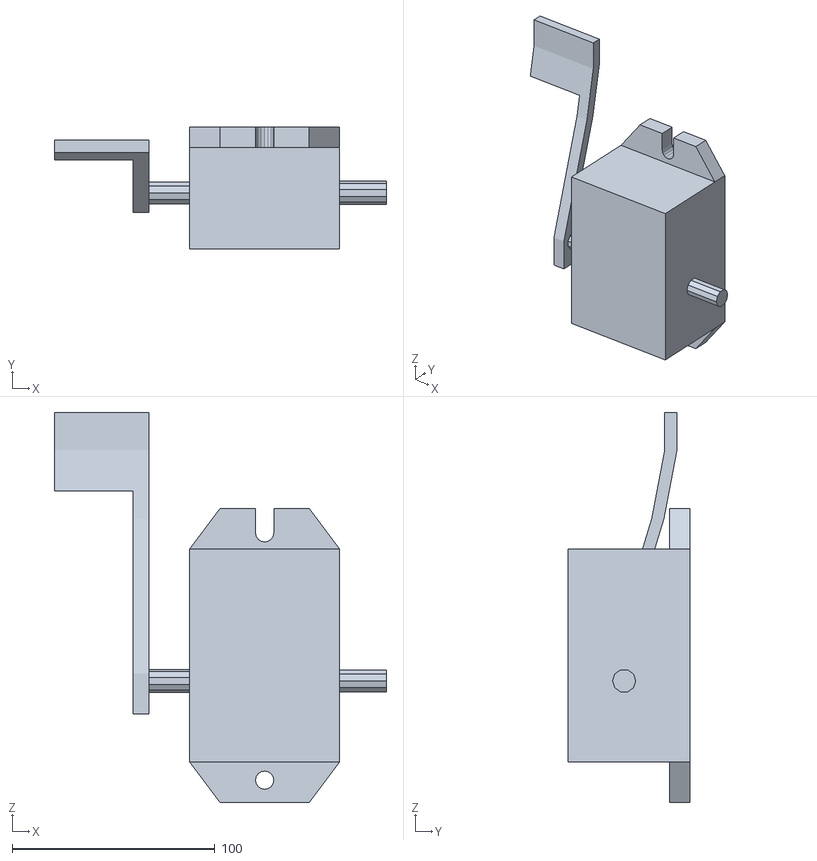
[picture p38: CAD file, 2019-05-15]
STL/pedal.stl
163.9 x 60.0 x 192.4

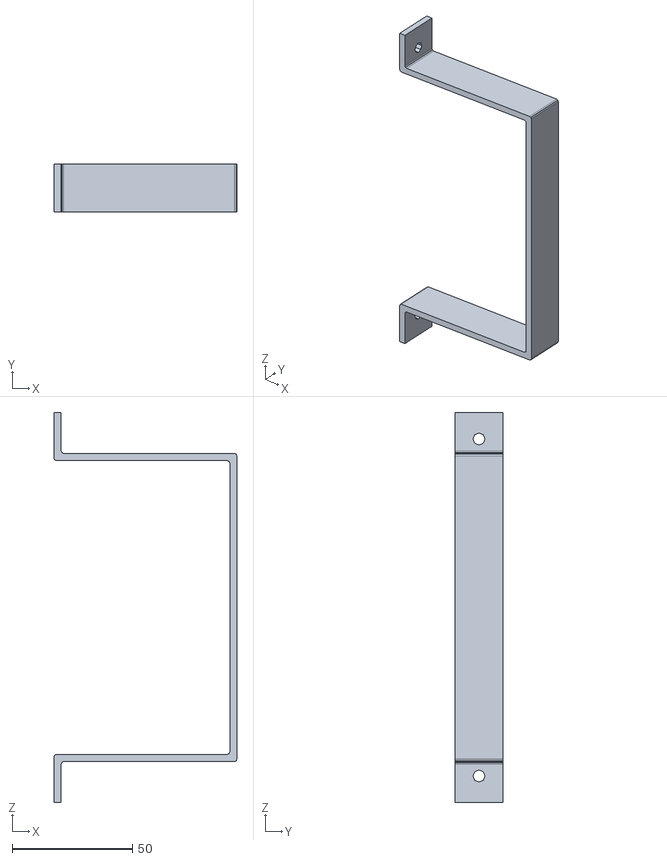
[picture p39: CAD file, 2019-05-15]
STL/nosilec_polnilca.stl
76.0 x 20.0 x 162.0

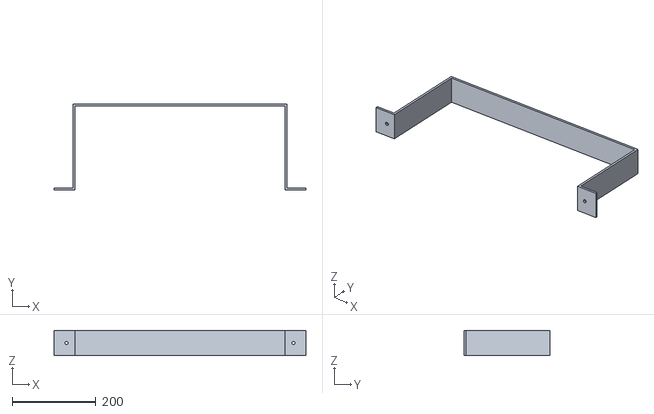
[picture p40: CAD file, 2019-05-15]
STL/nosilca_plata.stl
600.0 x 205.0 x 60.0

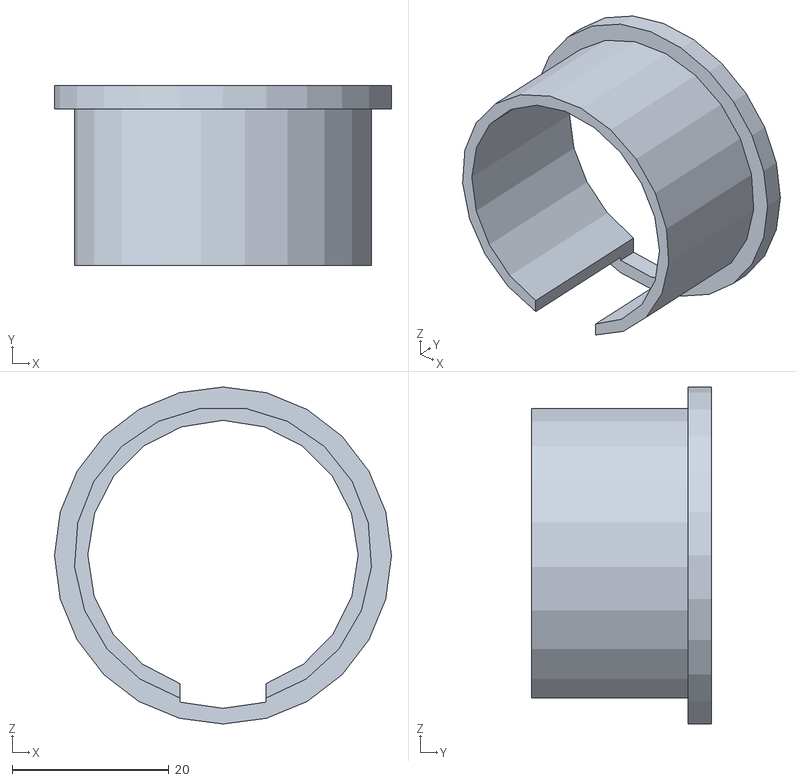
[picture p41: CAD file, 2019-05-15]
STL/nosilec_kljucavnice.stl
43.0 x 23.0 x 43.0

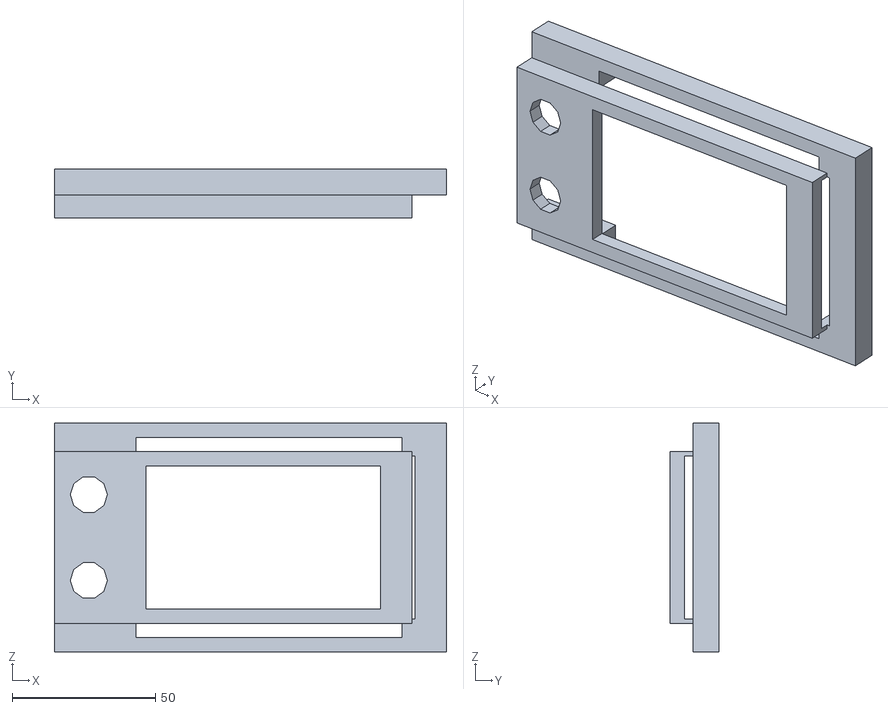
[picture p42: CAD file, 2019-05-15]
STL/nosilec_display1_2.stl
137.0 x 17.0 x 80.0

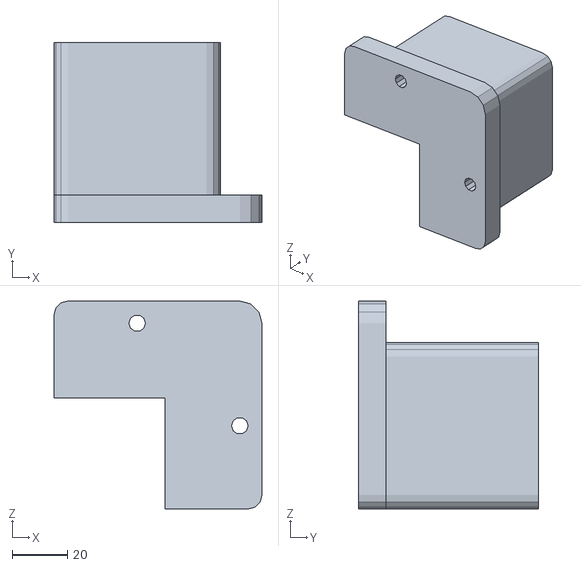
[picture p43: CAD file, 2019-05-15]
STL/vinkl_baterije.stl
75.0 x 65.0 x 75.0

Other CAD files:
STL/utinica0.stl
STL/stop_tipka.stl
STL/baterije_paket.stl

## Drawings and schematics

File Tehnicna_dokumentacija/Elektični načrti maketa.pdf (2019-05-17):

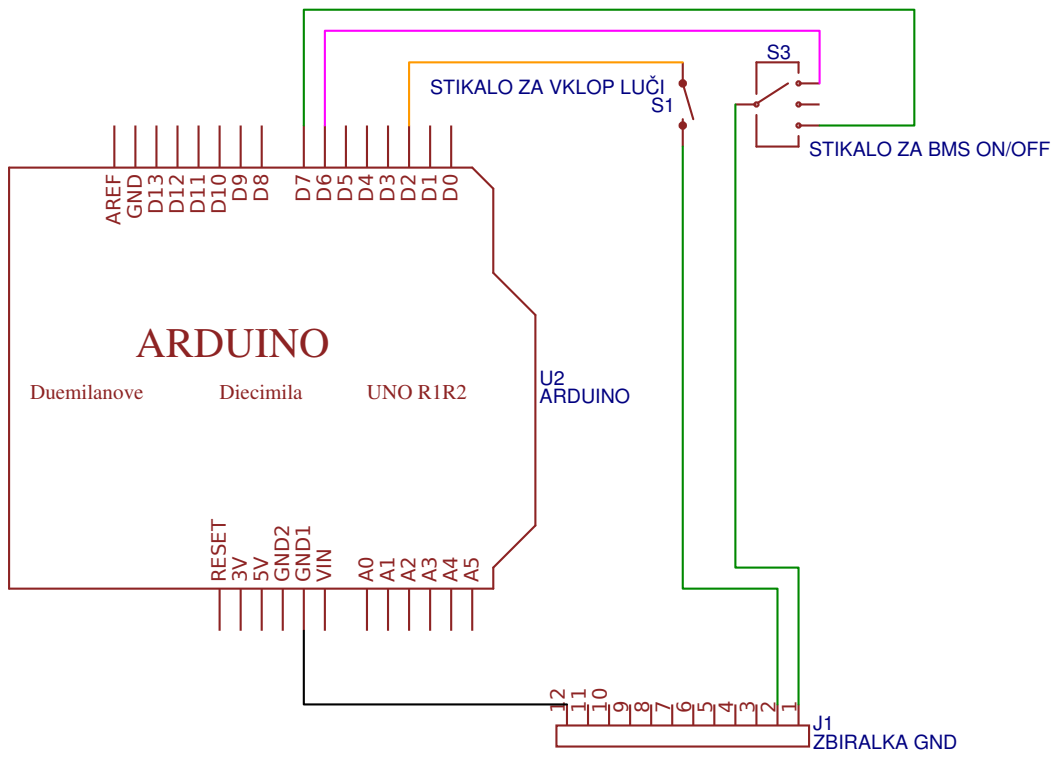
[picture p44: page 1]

STIKALO ZA VKLOP LUČI

STIKALO ZA BMS ON/OFF

Drawn By: Nik Vogrinec

# ARDUINO

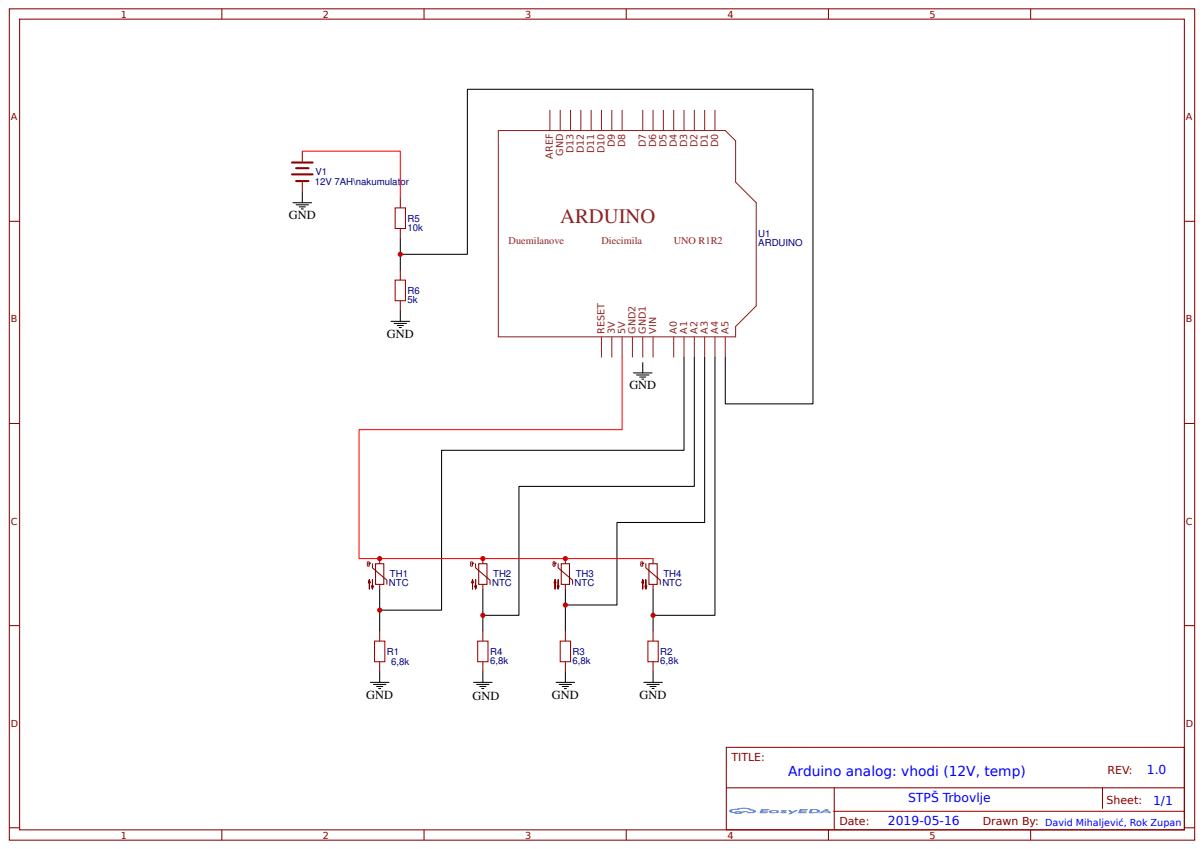
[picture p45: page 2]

David Mihaljević, Rok Zupan

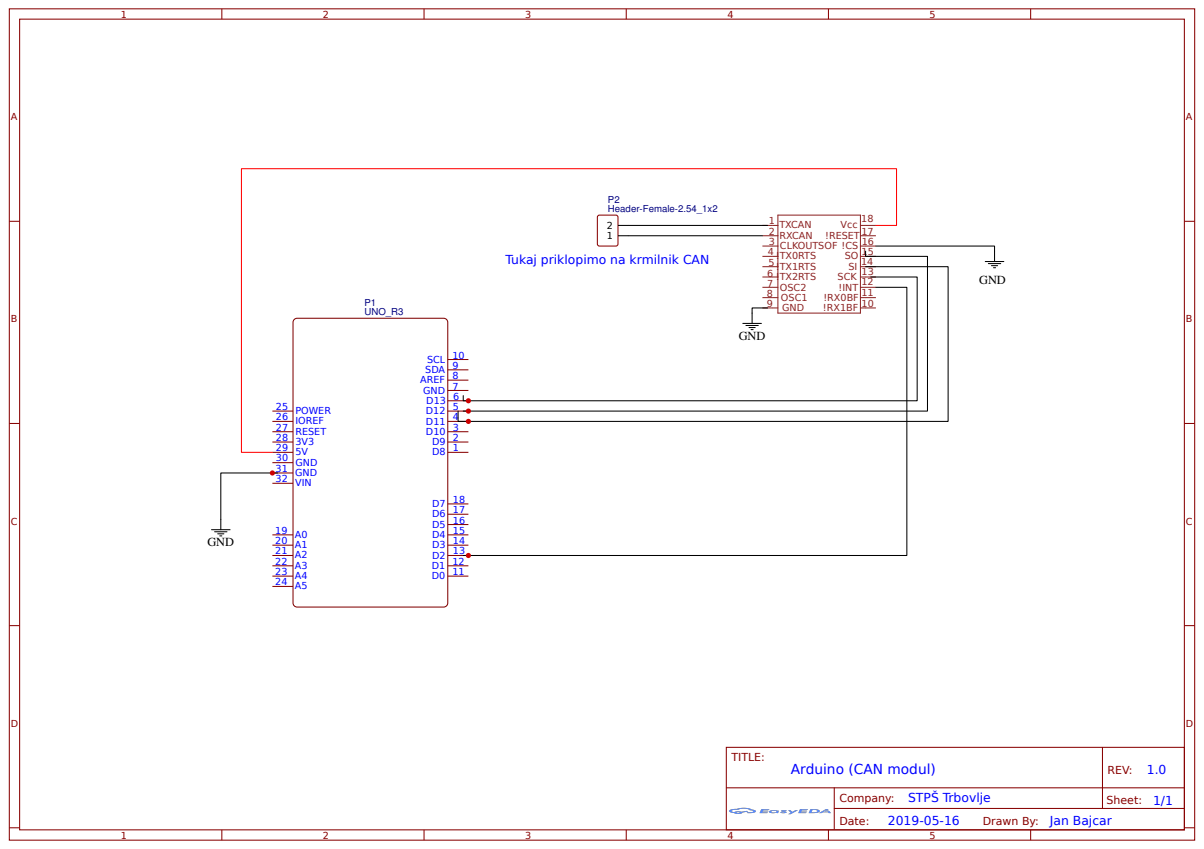
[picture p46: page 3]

Tukaj priklopimo na krmilnik CAN

Drawn By: Jan Bajcar

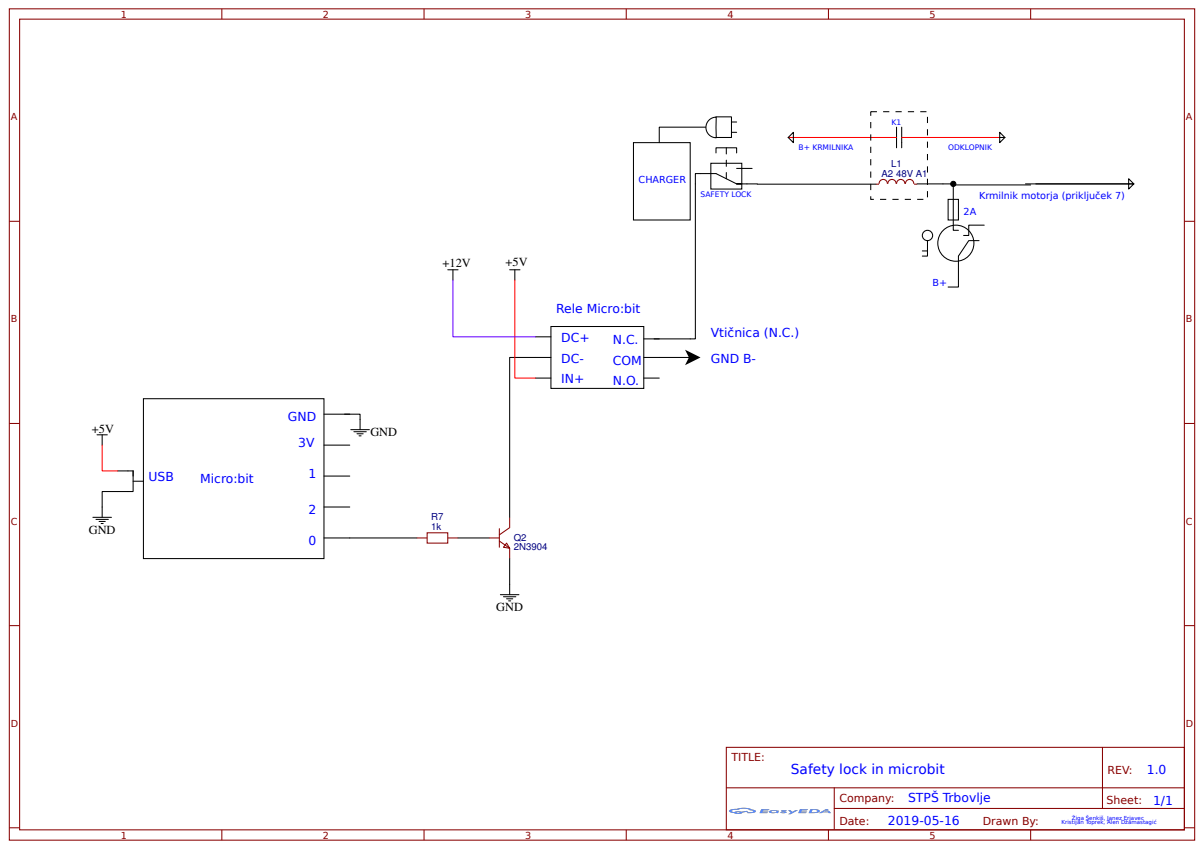
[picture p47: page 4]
TITLE:; Safety lock in microbit; REV: 1.0; Drawn By:; Žiga Šenkiš, Janez Erjavec; CHARGER; SAFETY LOCK; B+ KRMILNIKA; ODKLOPNIK; GND; Micro:bit; COM; USB; Vtičnica (N.C.); GND B-

Krmilnik motorja (priključek 7)

Rele Micro:bit

Kristijan Toprek, Alen Džamastagić

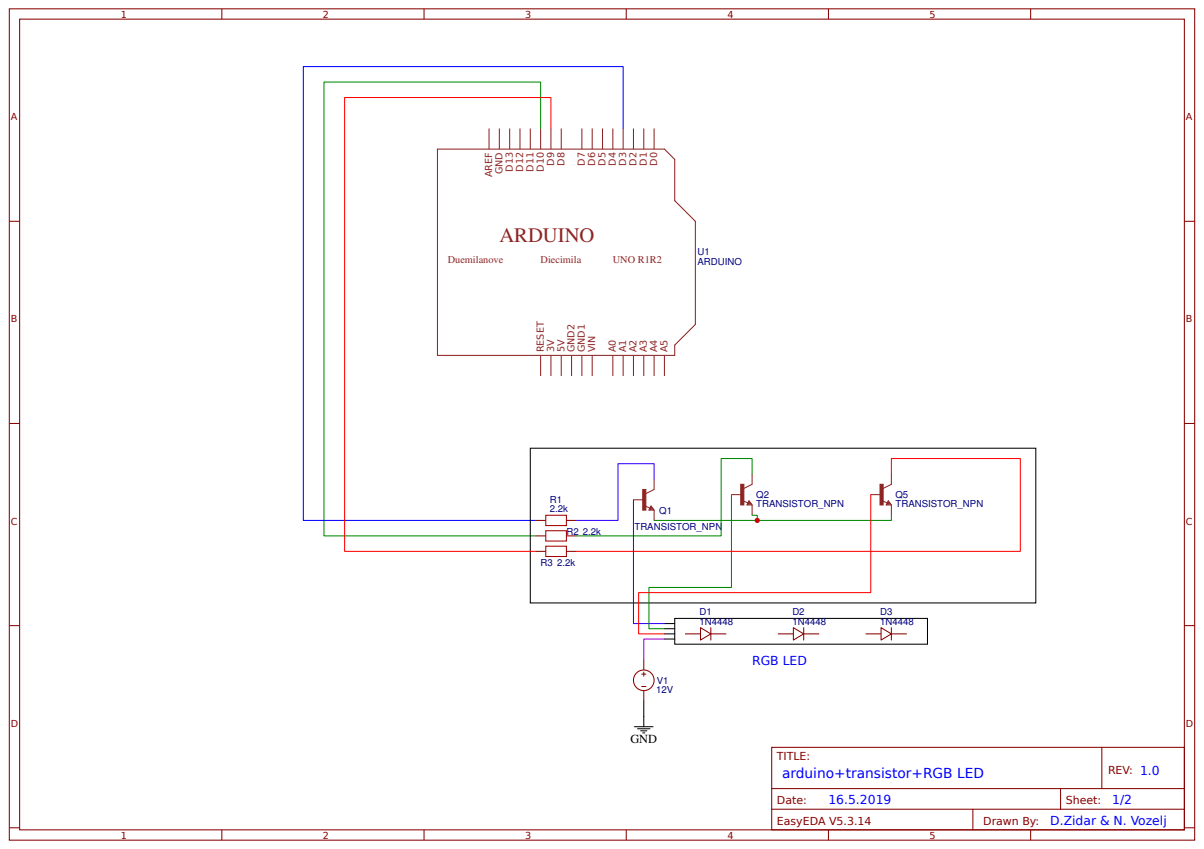
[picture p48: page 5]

# ARDUINO

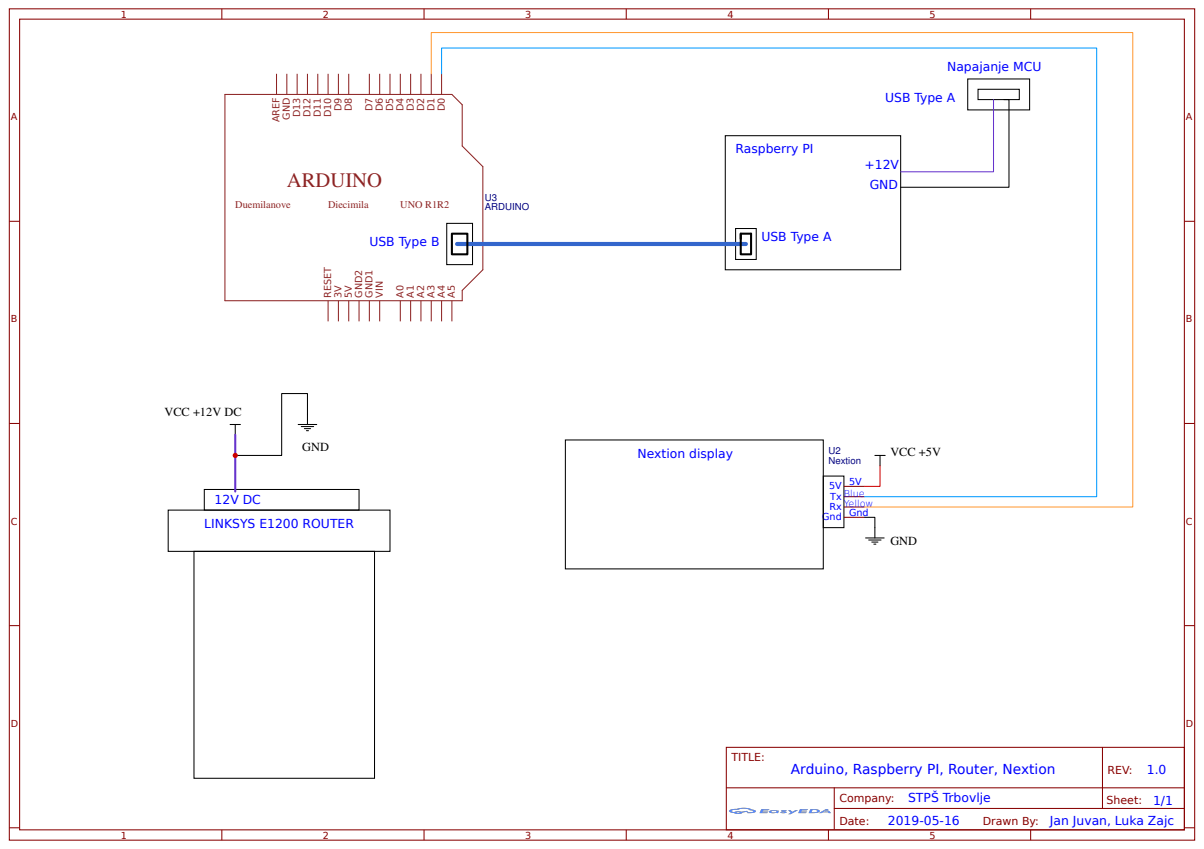
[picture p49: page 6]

Drawn By: Jan Juvan, Luka Zajc

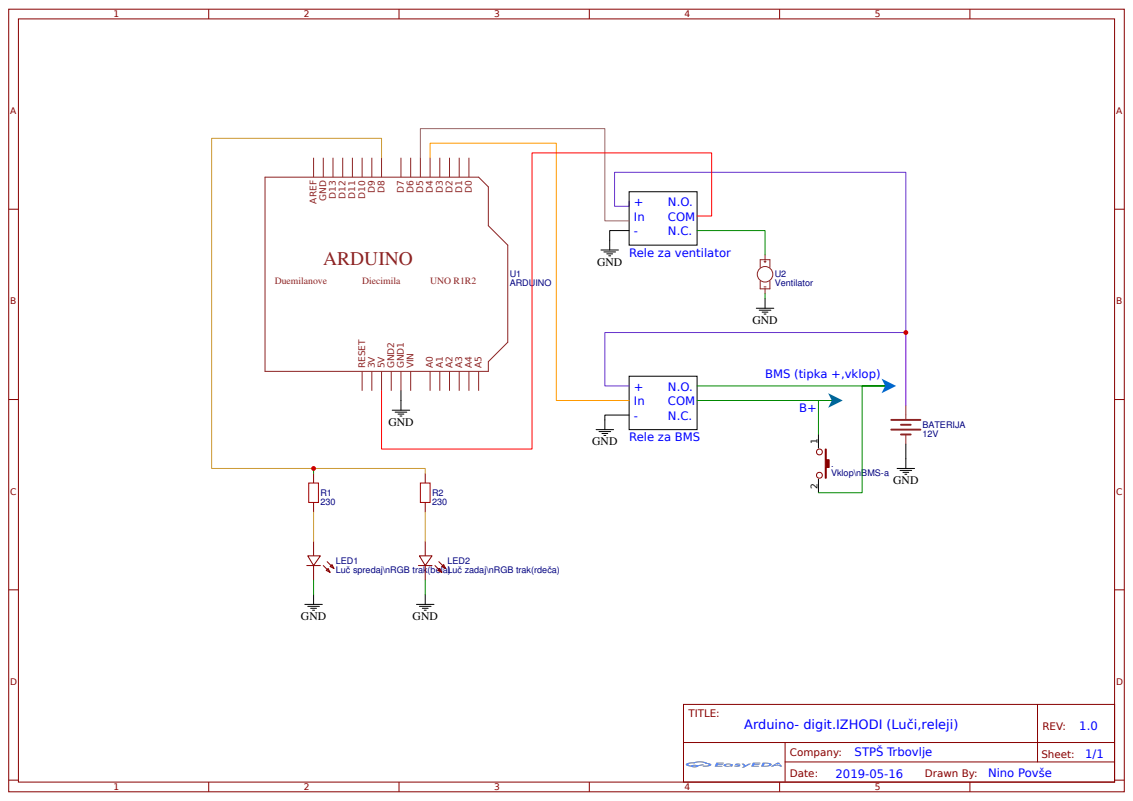
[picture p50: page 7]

LED1
Luč spredaj\nRGB trak(bela)

LED2
Luč zadaj\nRGB trak(rdeča)

Drawn By: Nino Povše

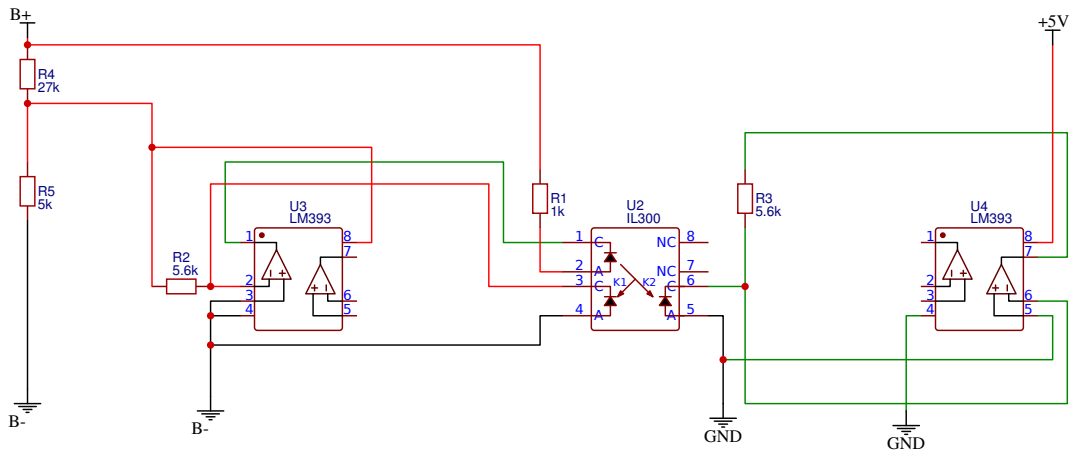
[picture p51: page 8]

Drawn By: Matic Rižner

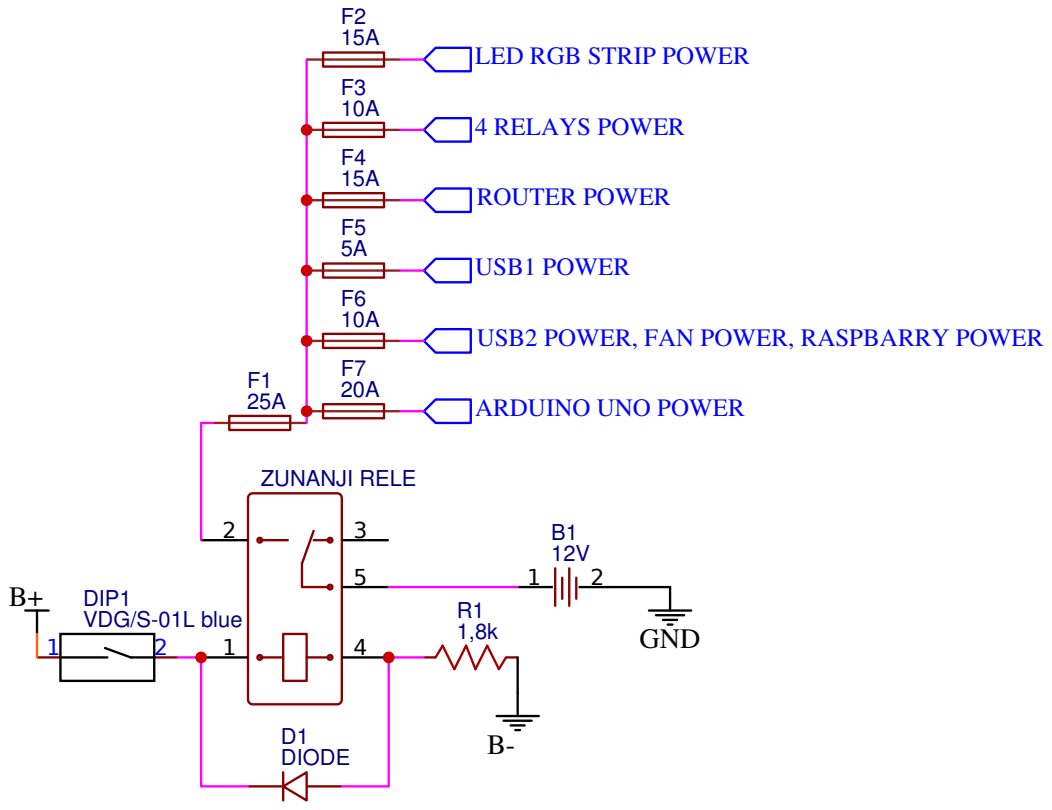
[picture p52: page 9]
TITLE:; 12V SISTEM, VAROVALKE; REV: 1.0; GND; VDG/S-01L blue; DIP1; ZUNANJI RELE; DIODE; USB1 POWER; ROUTER POWER; 4 RELAYS POWER

LED RGB STRIP POWER

USB2 POWER, FAN POWER, RASPBARRY POWER

ARDUINO UNO POWER

Drawn By: Luka Golob

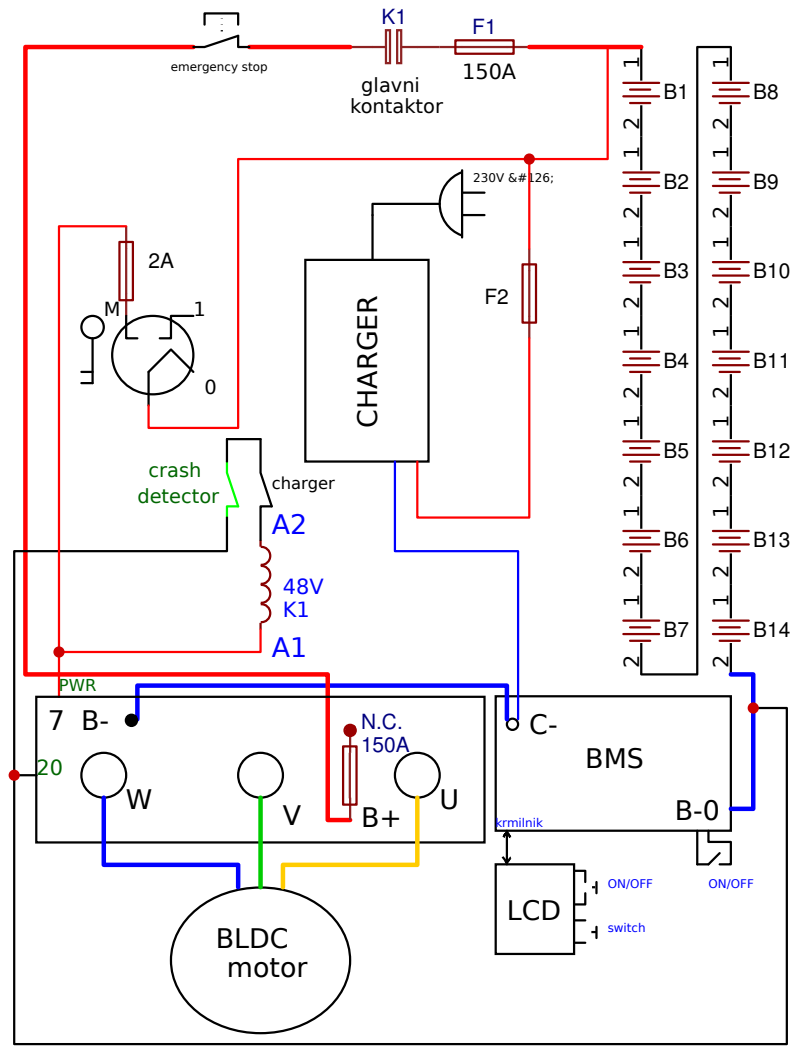
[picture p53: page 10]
TITLE:; Motor - krmilnik; REV: 1.0; BMS; LCD; ON/OFF; switch; CHARGER; BLDC motor; krmilnik; PWR; crash; charger; 150A emergency stop; detector; glavni kontaktor

Drawn By: Martin Gianini

+
B+

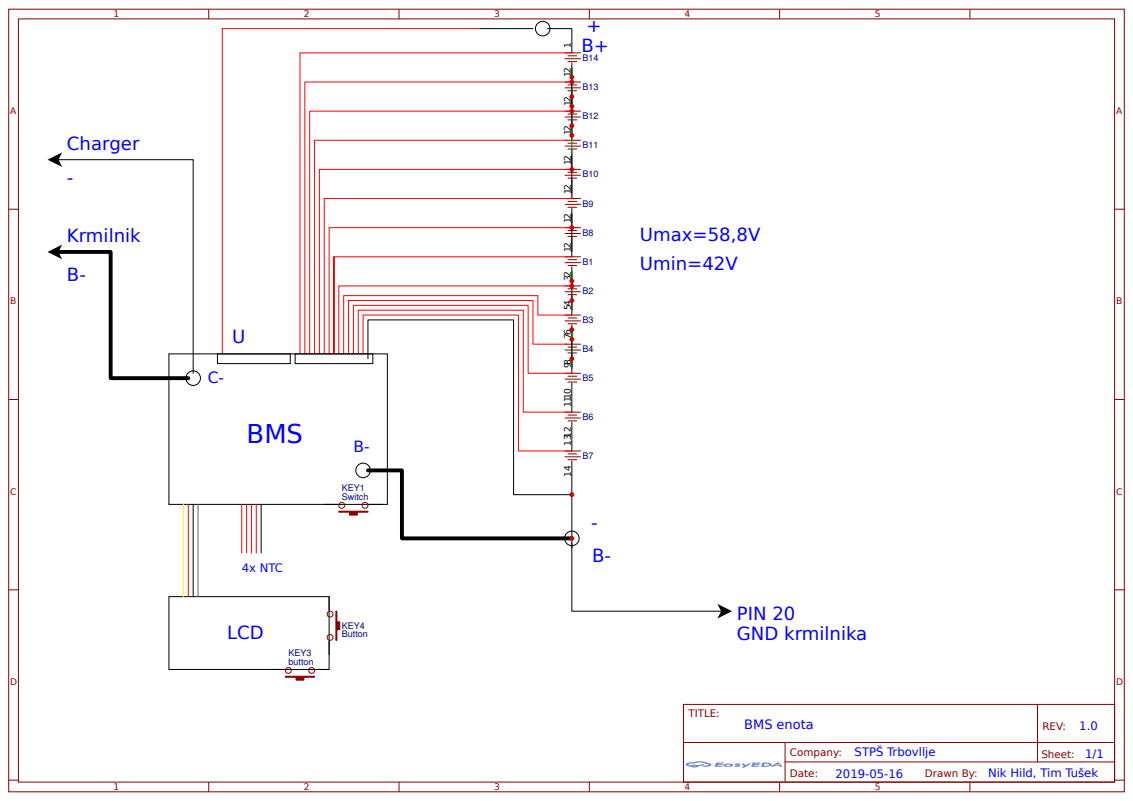
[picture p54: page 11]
TITLE:; BMS enota; REV: 1.0; BMS; LCD; button; KEY3; Button; KEY4; Switch; KEY1; Umax=58,8V Umin=42V; Charger; Krmilnik; PIN 20 GND krmilnika; 4x NTC

Company: STPŠ Trbovllje

Drawn By: Nik Hild, Tim Tušek

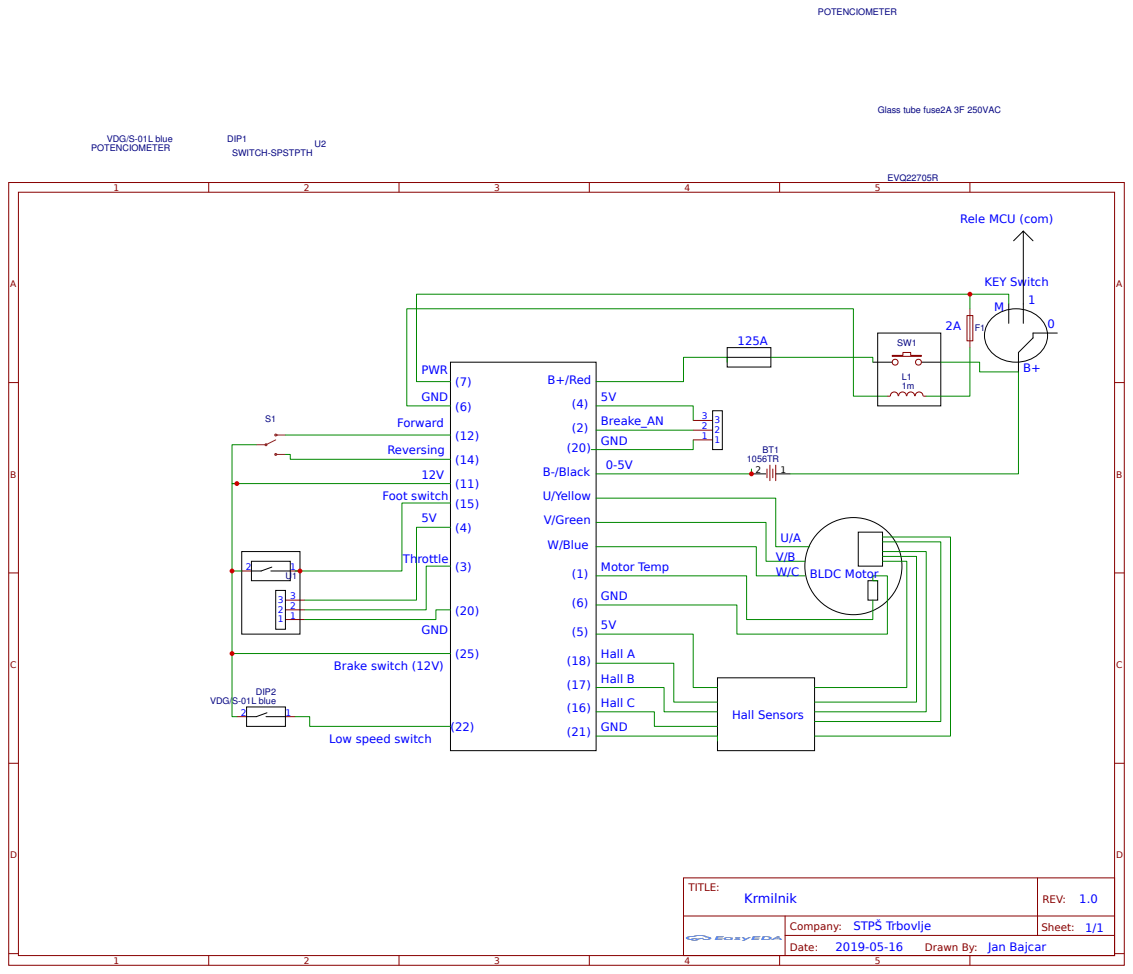
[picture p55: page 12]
TITLE:; Krmilnik; REV: 1.0; SWITCH-SPSTPTH; B+/Red; B-/Black; U/Yellow; V/Green; W/Blue; VDG/S-01L blue; DIP1; DIP2; POTENCIOMETER; BLDC Motor; Hall Sensors; PWR; GND; Forward; Reversing; Foot switch; Breake_AN GND; Motor Temp; EVQ22705R; Hall A; Hall B; Hall C; KEY Switch; Glass tube fuse2A 3F 250VAC; Brake switch (12V); Throttle

Rele MCU (com)

Low speed switch

Drawn By: Jan Bajcar

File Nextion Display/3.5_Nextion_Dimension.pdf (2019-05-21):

PCB1.60; 48.96(LCD AA); 54.94(OUTSIZE); 73.44(LCD AA); 94.10 85.50(LCD); 100.50(OUTSIZAE); LCD3.85 19.91

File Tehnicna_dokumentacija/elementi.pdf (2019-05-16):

1 | 2 | 3 | 4 | 5 | 6 | 7 | 8

A

Creo/Parametric; Merilo:; List; Ozn.; Sprememba; Datum; Ime; Material:; Št. risbe:; Nadom:; Nadom. z:; Masa:; Kg Tolerance odprtih; mer; Površinska hrapavost

Datum | Ime | Naziv: ELEMENTI

Izdel. | 14.12.18 | X
Kontr.
K.std.

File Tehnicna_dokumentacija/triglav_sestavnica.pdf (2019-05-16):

Creo/Parametric; List; Ozn.; Sprememba; Datum; Ime; Naziv:; Št. risbe:; Nadom:; Nadom. z:; TRIGLAV_SESTAVNICA; DISPLAY_75_50_3; OHISJE_BATERIJ1; STPŠ

Poz | Kos | En | Naziv in mere | Koda/standard | Opomba
13 | 1 | | STOP_TIPKA | X | X
12 | 1 | | SKATLA_263_185_95 | X | X
11 | 1 | | POLNILEC_182_94_52 | X | X
10 | 1 | | PEDAL | X | X

8 | 1 | OHISJE_BATERIJ | X | X
7 | 2 | NOSILEC | X | X
6 | 1 | MOTOR | X | X
5 | 1 | KRMILNIK_BMS_160_72_30X | | X
4 | 1 | KONTROLER_KLS7230S | X | X
3 | 2 | KOLO
2 | 1 | ELAVTO | X | X

Datum | Ime | 7:100 Merilo: | 99,038 Masa: Kg

Izdel. | 05.11.18 | X
kontr.
K.std.

Creo/Parametric; Merilo:; List; Ozn.; Sprememba; Datum; Ime; Material:; Št. risbe:; Nadom:; Nadom. z:; Masa:; Kg Tolerance odprtih; mer; Površinska hrapavost; STPŠ; inox - Al?

Datum | Ime | Naziv: TRIGLAV_SESTAVNICA

Izdel. | 14.12.18 | 3.B
Kontr.
K.std.

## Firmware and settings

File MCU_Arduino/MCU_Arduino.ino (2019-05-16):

#include <doxygen.h>

//#include <Nextion.h>
//#include <NexTouch.h>

#include <NexGauge.h>
#include <NexPicture.h>
#include <NexProgressBar.h>

/* Tipke
#include <NexButton.h>
#include <NexDualStateButton.h>
*/

//#include <NexConfig.h>
//#include <NexCrop.h>





int BatteryVoltagePin0 = 0;   //A0 vhod za IL300 opto linear pretvornik za Li-ion
// A0 pin za branje napetosti baterije +B preko sonde/delilnika
int ThermistorPin1 = 1;     //A1 vhod 
int ThermistorPin2 = 2;     //A2 vhod
int ThermistorPin3 = 3;     //A3 vhod
int ThermistorPin4 = 4;     //A4 vhod
int voltBatPin = 5;     //A5 vhod za 12V baterijo

// Avto luč
int Luc = 8; // Pin 8 sprednja in zadnja luč
int StikaloLuc = 2; // Pin 2 za vklop luči spredaj in zadaj via stikalo
int Luc_stat = 0;

int V1, V2, V3, V4, V0;        
float R1 = 6800;
float logR21, logR22, logR23, logR24, R21, R22, R23, R24, T21, T22, T23, T24, T11, T12, T13, T14, Tf, V0Bat;
float c1 = 1.163854283e-03, c2 = 2.489458305e-04, c3 = 1.130393822e-07;
float batVoltage = 0;
int batLow12 = 0; //12V baterija
char dataString[50] = {0};

int VklopBMS = 4; //Pin 4 za vklop BMS

//Vžig in izklop BMS
int On_BMS = 6;  
int Off_BMS = 7;
int Vzig_BMS = 1;

//RGB control PWM
int RGB_G = 3;
int RGB_R = 10;
int RGB_B = 9;

//Fan kontrol
int Fan_bat = 5;
int Fan_stat = 0; //Signal za pie 1 ali 0

//Definirati pine 11, 12 in 13 za SPI komunikacijo za CAN modul

//Zaslon
NexProgressBar j0 = NexProgressBar(0, 4, "j0"); //Graf za prikaz temperature krmilnik
NexProgressBar j1 = NexProgressBar(0, 1, "j1"); //Graf za prikaz temperature baterije
NexProgressBar j2 = NexProgressBar(0, 2, "j2"); //Graf za prikaz temperature BMS
NexProgressBar j3 = NexProgressBar(0, 3, "j3"); //Graf za prikaz temperature motorja
NexProgressBar j4 = NexProgressBar(0, 7, "j4"); //Stanje polnosti 12V baterije
NexProgressBar j5 = NexProgressBar(0, 6, "j5"); //Stanje luči
NexProgressBar j6 = NexProgressBar(0, 8, "j6"); //Stanje ventilatorja za hlajenje baterije

NexGauge z0 = NexGauge(0, 5, "z0"); //Števec za prikaz napetosti baterije

void setup() {
 delay(400);
 Serial.begin(9600);
 pinMode(Luc, OUTPUT);
 pinMode(Fan_bat, OUTPUT);
 pinMode(StikaloLuc, INPUT_PULLUP); // Definirana za vklop sprednje luči
 pinMode(VklopBMS, OUTPUT);
 pinMode(On_BMS, INPUT_PULLUP);
 pinMode(Off_BMS, INPUT_PULLUP);
 digitalWrite(VklopBMS, HIGH);  //Vklop  bms za 3s
 delay(3200);
 digitalWrite(VklopBMS, LOW);  //Izklop tipke --> BMS je sedaj vklopljen
 nexInit();
}

void loop() {
//12v BATTERY setup
batVoltage = ((analogRead(voltBatPin)*5.0)/1023.0)*2.767;
if (batVoltage<=11.8){
  batLow12 = 1;
}
else{
  batLow12 = 0;
}
//temp. 1 - Krmilnik:
V1 = analogRead(ThermistorPin1);
R21 = R1 * (1023.0 / (float)V1 - 1.0);
logR21 = log(R21);
T11 = (1.0 / (c1 + c2*logR21 + c3*logR21*logR21*logR21));
T21 = T11 - 273.15;
//temp. 2 - Baterijska:
V2 = analogRead(ThermistorPin2);
R22 = R1 * (1023.0 / (float)V2 - 1.0);
logR22 = log(R22);
T12 = (1.0 / (c1 + c2*logR22 + c3*logR22*logR22*logR22));
T22 = T12 - 273.15;
//temp. 3 - Motor:
V3 = analogRead(ThermistorPin3);
R23 = R1 * (1023.0 / (float)V3 - 1.0);
logR23 = log(R23);
T13 = (1.0 / (c1 + c2*logR23 + c3*logR23*logR23*logR23));
T23 = T13 - 273.15;
//temp. 4 - BMS:
V4 = analogRead(ThermistorPin4);
R24 = R1 * (1023.0 / (float)V4 - 1.0);
logR24 = log(R24);
T14 = (1.0 / (c1 + c2*logR24 + c3*logR24*logR24*logR24));
T24 = T14 - 273.15;
//napetost +B baterije --> od 40,6V ÷ 58,8V naj bi se izpisalo, ko merimo ...
V0 = analogRead(BatteryVoltagePin0);
V0Bat= V0; //vrednosti so od 0 do cca 45

float V0BatDisplay = (V0Bat-28)*12.857;
//Serial.println(V0BatDisplay);
//preko USB porta (UART) pošiljamo v taki obliki za Raspberry PI:
delay(200);
Serial.print(";TempController:"+String(T21)+";TempBattery:"+String(T22)+";TempMotor:"+String(T23)+";TempBMS:"+String(T24)+";BatVoltage:"+String(V0Bat)+";fan:"+String(Fan_stat)+";BMS_start:"+String(Vzig_BMS)+";"+";AkuVoltage:"+String(batVoltage)+";");

//Obvezno nastavljanje prvega števca dvakrat

j0.setValue(T21); //KRMILNIK
j0.setValue(T21); //KRMILNIK
j1.setValue(T22); //BATERIJE
j3.setValue(T23); //MOTOR
j2.setValue(T24); //BMS
j4.setValue(batLow12*100);  //indikator 12V BAT
j5.setValue(Luc_stat*100);  //indikator luci
j6.setValue(Fan_stat*100);  //indikator ventilator
z0.setValue(V0BatDisplay); //NAPETOST

//serial prenos povzroča resetiranje Arduina na točno 1 min!

/* RGB: 
 42V    <  Rdeča   < 45.35V, --> RGB_R=255, RGB_G=0,   RGB_B=0
 45.36V <  Oranžna < 48.71V, --> RGB_R=255, RGB_G=127, RGB_B=0
 48.72V <  Rumena  < 52.07V, --> RGB_R=255, RGB_G=255, RGB_B=0
 52.08V <  Zelena  < 55.43V, --> RGB_R=0,   RGB_G=255, RGB_B=0
 55.44V <  Modra   < 58.8V   --> RGB_R=0,   RGB_G=127, RGB_B=255
*/

//V0 = 58;

if (V0Bat <= 29) {                       //Rdeča
  analogWrite(RGB_R, 255);
  analogWrite(RGB_G, 0);
  analogWrite(RGB_B, 0);
  }
else if (V0Bat > 29 and V0Bat <= 32) {   //Oranžna
  analogWrite(RGB_R, 255);
  analogWrite(RGB_G, 40);
  analogWrite(RGB_B, 0);
  }
else if (V0Bat >  32 and V0Bat <= 36) {  //Rumena
  analogWrite(RGB_R, 255);
  analogWrite(RGB_G, 175);
  analogWrite(RGB_B, 0);
  }
else if (V0Bat >  36 and V0Bat <= 39) {  //Zelena
  analogWrite(RGB_R, 0);
  analogWrite(RGB_G, 255);
  analogWrite(RGB_B, 0);
  }
else {                                    //Modra
  analogWrite(RGB_R, 0);
  analogWrite(RGB_G, 127);
  analogWrite(RGB_B, 255);
  }
  
// ----------------------------------------------Luči za avto--------------------------------------------

if (digitalRead(StikaloLuc) == LOW){ 
  digitalWrite(Luc, HIGH);
  Luc_stat = 1;
  
  }
else if (digitalRead(StikaloLuc) == HIGH){
  digitalWrite(Luc, LOW);
  Luc_stat = 0;
}

//---------------------------------------------Vklop BMS--------------------------------------------------

if(digitalRead(On_BMS) == LOW and Vzig_BMS == 0){
  digitalWrite(VklopBMS, HIGH);  //Vklop  bms za 3s
  delay(3000);
  digitalWrite(VklopBMS, LOW);  //Izklop tipke --> BMS je sedaj vklopljen
  Vzig_BMS = 1;
  }
else if(digitalRead(Off_BMS) == LOW and Vzig_BMS == 1){
  Vzig_BMS = 0;
  digitalWrite(VklopBMS, HIGH);  //Vklop  bms za 5s
  delay(6500);
  digitalWrite(VklopBMS, LOW);  //Izklop tipke --> BMS je sedaj izklopljen
  }
  
//-------------------------------------------------FAN---------------------------------------------------

if(T22 > 40){
  digitalWrite(Fan_bat, HIGH);
  Fan_stat = 1;
}
else if(T22 < 39.99){
  digitalWrite(Fan_bat, LOW);
  Fan_stat = 0;
}





}

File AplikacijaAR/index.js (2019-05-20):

const Gpio = require('onoff').Gpio;
const exec = require('child_process').exec
const SerialPort = require('serialport');
const fs = require('fs');
const express = require('express');
const app = express();
const port = new SerialPort('/dev/ttyACM0', () => {
console.log('Port Opened');
});

const parsers = SerialPort.parsers;

const parser = new parsers.Readline({
delimiter: ';'
});
var LED = new Gpio(18, 'out');

let data = 'null;null';


function sendSensorData(data){

	data['time'] = Date.now();
	console.log(data);

	/*fs.readFile('/home/pi/eleAvto/nodeServer/log.json', function (err, log) {
		var json = {};
		if(!err){
			var json = JSON.parse(log);
		}
		json.push(data);    
		fs.writeFile("/home/pi/eleAvto/nodeServer/log.json", JSON.stringify(json,null,2), function(err){
		  if (err) throw err;
		  console.log('The "data to append" was appended to file!');
		});
	});*/

	dataStatus = data;
	
}


let dataSet={};
let dataLength = 8;
let dataStatus = {};

function retrieveData(dt){
	if(!dt.includes(':') || dt.includes('j0')) return;
	

	data = dt.split(':');
	dataSet[data[0]] =  parseFloat(data[1]);

	if(data[0] == 'AkuVoltage'){
		if(Object.keys(dataSet).length == dataLength){
			sendSensorData(dataSet)
		}
		dataSet={};
	}

	LED.writeSync(1);
	setTimeout(function(){
		LED.writeSync(0);
	}, 100);
}



port.pipe(parser);
parser.on('data', retrieveData);
LED.writeSync(0);

app.get('/', (req, res) => {
	res.json((dataStatus));
});

app.get('/log', (req, res) => {
	fs.readFile('/home/pi/eleAvto/nodeServer/log.json', function(err, log){
		if(err){ 
			res.end();
			throw err;
		}
		res.json(JSON.parse(log));
	});
});

const server = app.listen(80, () => {
	console.log(`Express running → PORT ${server.address().port}`);
  });

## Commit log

2019-05-15 APK program za BMS na andorid
    Namestitev APK na pametni telefon, kjer se via Bluetooth poveže z BMS. Geslo za povezavo BMS-a je 1234.
2019-05-15 STL datoteke
    [baterije_paket.stl, elavto.stl, kolo.stp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]
2019-05-15 Slikovni prikaz komponent - promo material
2019-05-16 STL datoteke posameznih elementov
2019-05-16 STL celotne makete
    [triglav_11.stl]
2019-05-16 Program za MCU
    - Krmiljenje luči, relejev, ventilatorja
    - Vklop/izklop BMS-a
    - Krmiljenje RGB LED traku
    - Merjenje temperatur (4 x NTC senzor)
    - Merjenje napetosti akumulatorja (12V)
    - Merjenje napetosti Li-Ion sklopa z IL300
    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
2019-05-16 PDF in ostali informativni material
2019-05-21 Navodila priključitve BMS enote (ANG)
